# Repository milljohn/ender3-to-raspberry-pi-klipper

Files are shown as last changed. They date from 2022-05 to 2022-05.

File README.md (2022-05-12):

# ender3-to-raspberry-pi-klipper

Raspberry Pi Zero hat that supplies power via Ender 3V2 LCD cable for Klipper. NOTE: this seems to only work a Pi Zero, not a Pi 4. Not tested with a Pi 3 yet.

I made a quick version of this on protoboard, but I'm planning on making a few of these for printers at work and I wanted something a little cleaner and easier to put together.

I originally designed this as a hat, but after thinking about the prototype, it would be better just to make an adapter with crimp connectors.

This was originally posted [here](https://www.reddit.com/r/klippers/comments/q5cu20/how_to_connect_creality_v422_board_to_pi_using/).

## The PCB

The latest version is pi_hat_v2, though it is no longer a hat. I generated the cam files in pcb_files.zip. You can see the rendering below.

### Components
- 1 - 5 position, 2.54mm pitch female (socket) header
- 1 - 10 position, 2 rows, 2.54mm pitch male (pin) 90 degree header

NOTE: I used a 90 degree header so the drawer would close. It will work with straight headers, but you may have clearance issues.

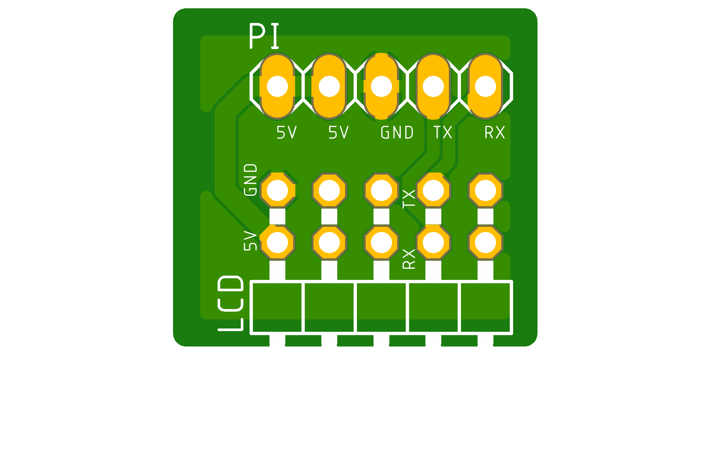
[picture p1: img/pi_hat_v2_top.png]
board top

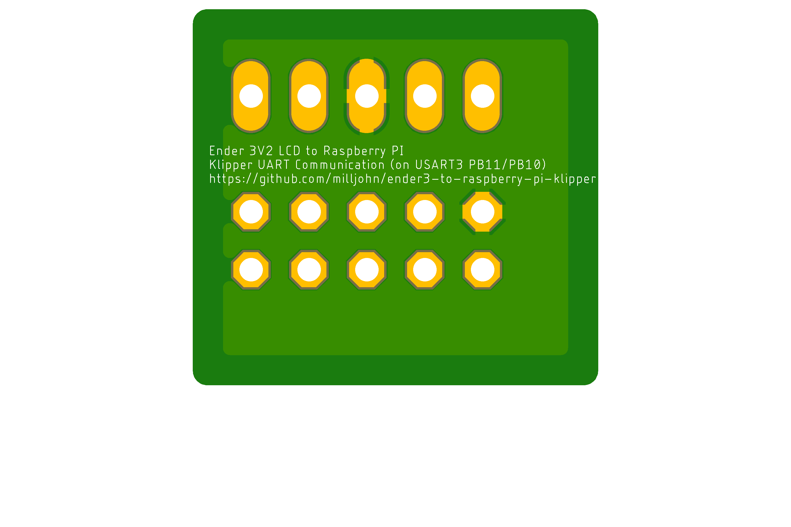
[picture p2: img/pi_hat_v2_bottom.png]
board bottom


## Klipper Configuration
If you are just starting out, [this guide](https://www.reddit.com/r/klippers/comments/kj2h5r/stepbystep_guide_for_ender_3_v2_klipper_w_bltouch/) will probably be helpful. I've tried to document the steps I took to [setup my printer](#fluidd-pi-configuration)

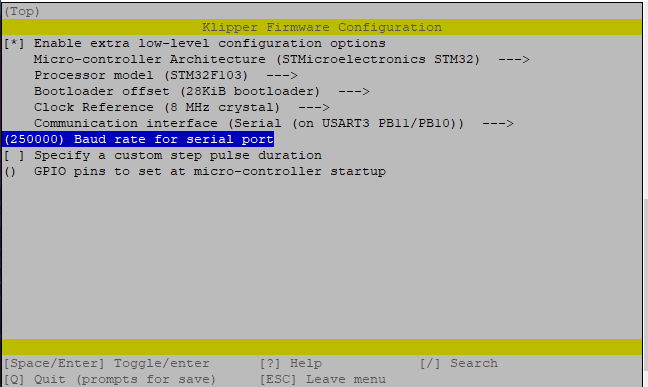
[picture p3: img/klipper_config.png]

[Klipper Firmware Configuration](https://i.imgur.com/JYTF8Xj.png)

Add ``serial = /dev/ttyAMA0`` to `printer.cfg`. Your serial port might be different. You can check by power on the Pi via USB and typing `ls /dev` and then comparing it to the list when connected with the ribbon cable. Mine was actually `/dev/ttyS0`. 

## Rasperry Pi Configuration
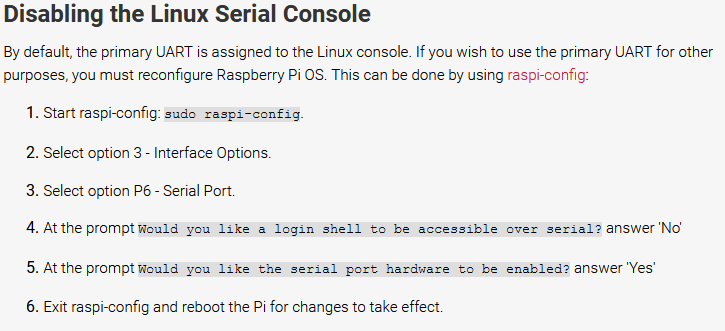
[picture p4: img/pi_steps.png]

[Disabling the Linux Serial Console](https://i.imgur.com/P6BS6GC.png)

This may be needed as well:
```shell
sudo echo dtoverlay=disable-bt >> /boot/config.txt
```

## Ender 3V2 Drawer 
I really like this drawer mount.

[Ender 3 v2 Hidden OctoPi Mount](https://www.thingiverse.com/thing:5201485)

Pi Zero drawer mount

## Fluidd Pi Configuration

These are the steps I took to setup Fluidd Pi

1. Burn Fluidd Pi [image](https://github.com/fluidd-core/FluiddPi/releases/latest) to SD Card 
2. Boot the Raspberry Pi
    - Add ssh keys to pi and update `~/.ssh/config`
      - on host: `ssh-keygen -t rsa -b 4096`, I chose no password and saved the file as 3dprinters
      - `mv ~/.ssh/3dprinters ~/.ssh/3dprinters.pem`
      - add the following to ~/.ssh/config
      ```
      host ender3.1
      hostname <raspi-ip-address>
      identityfile ~/.ssh/3dprinters.pem
      user pi

      ```
      - copy the public key to the pi
      ```
      sftp ender3.1
      mkdir -p .ssh
      put ~/.ssh/3dprinters.pub
      bye

      ssh ender3.1
      cd .ssh
      cat 3dprinters.pub >> authorized_keys
      exit
      ```
      - next time you `ssh ender3.1` it will login without a password.

    - `cd klipper && make menuconfig && make`
        - the default for usb is as follows
        
            1. Uncheck `Enable extra low-level configuration options`.
            2. Set processor architecture to `STMicroelectronics STM32`.
            3. Set processor model to `STM32F103`.
            4. Set bootloader offset to `28KiB bootloader`.
            5. Uncheck the other two options (`Use USB` and `Use CAN`).
            6. Save and exit.
        - if setting up serial over LCD cable, use the guide at the top of the page.
    - sftp and copy `~/klipper/out/klipper.bin` to SD card
        - insert into printer and turn on
    - run `~/moonraker/scripts/set-policykit-rules.sh`
    - `cp ~/klipper/config/printer-creality-ender3-v2-2020.cfg ~/klipper_config/printer.cfg`
    - add the lines below to `~/klipper_config/printer.cfg`
    - go to `http://<raspberrypi-ip-address>`
        - Check that everything is working with USB or serial
        - Tail logs, `tail -f ~/klipper_logs/klippy.log` and `tail -f ~/klipper_logs/moonraker.log`
3. `sudo raspi-config`
    - System options
        - setup wireless lan if you didn't already
        - change the default password
        - change the hostname if you want
    - Interface Option
        - ssh
        - serial port
            - no login over serial
            - enable hardware serial port
        - localization options (optional)
            - set to utf-8 and local timezome
    - reboot
    - run `sudo apt update && sudo apt upgrade -y`
4. Check the web interface to see if everything is working
    - check logs if something isn't working

Add this to the `printer.cfg`. I'm not sure why it isn't there by default, but it was frustrating trying to figure out that this was needed.
```
[virtual_sdcard]
path: ~/gcode_files

[display_status]

[pause_resume]

[gcode_macro PAUSE]
description: Pause the actual running print
rename_existing: PAUSE_BASE
# change this if you need more or less extrusion
variable_extrude: 1.0
gcode:
  ##### read E from pause macro #####
  {% set E = printer["gcode_macro PAUSE"].extrude|float %}
  ##### set park positon for x and y #####
  # default is your max posion from your printer.cfg
  {% set x_park = printer.toolhead.axis_maximum.x|float - 5.0 %}
  {% set y_park = printer.toolhead.axis_maximum.y|float - 5.0 %}
  ##### calculate save lift position #####
  {% set max_z = printer.toolhead.axis_maximum.z|float %}
  {% set act_z = printer.toolhead.position.z|float %}
  {% if act_z < (max_z - 2.0) %}
      {% set z_safe = 2.0 %}
  {% else %}
      {% set z_safe = max_z - act_z %}
  {% endif %}
  ##### end of definitions #####
  PAUSE_BASE
  G91
  {% if printer.extruder.can_extrude|lower == 'true' %}
    G1 E-{E} F2100
  {% else %}
    {action_respond_info("Extruder not hot enough")}
  {% endif %}
  {% if "xyz" in printer.toolhead.homed_axes %}
    G1 Z{z_safe} F900
    G90
    G1 X{x_park} Y{y_park} F6000
  {% else %}
    {action_respond_info("Printer not homed")}
  {% endif %}

[gcode_macro RESUME]
description: Resume the actual running print
rename_existing: RESUME_BASE
gcode:
  ##### read E from pause macro #####
  {% set E = printer["gcode_macro PAUSE"].extrude|float %}
  #### get VELOCITY parameter if specified ####
  {% if 'VELOCITY' in params|upper %}
    {% set get_params = ('VELOCITY=' + params.VELOCITY)  %}
  {%else %}
    {% set get_params = "" %}
  {% endif %}
  ##### end of definitions #####
  {% if printer.extruder.can_extrude|lower == 'true' %}
    G91
    G1 E{E} F2100
  {% else %}
    {action_respond_info("Extruder not hot enough")}
  {% endif %}  
  RESUME_BASE {get_params}

[gcode_macro CANCEL_PRINT]
description: Cancel the actual running print
rename_existing: CANCEL_PRINT_BASE
gcode:
  TURN_OFF_HEATERS
  CANCEL_PRINT_BASE
```

moonraker.conf
```
[server]
host: 0.0.0.0
port: 7125
enable_debug_logging: False

[file_manager]
config_path: ~/klipper_config
log_path: ~/klipper_logs

[data_store]
temperature_store_size: 600
gcode_store_size: 1000

[authorization]
force_logins: True
cors_domains:
  *.local
  *.lan
  *://app.fluidd.xyz

trusted_clients:
  10.0.0.0/8
  127.0.0.0/8
  169.254.0.0/16
  172.16.0.0/12
  192.168.0.0/16
  FE80::/10
  ::1/128

# enables partial support of Octoprint API
[octoprint_compat]

# enables moonraker to track and store print history.
[history]

# this enables moonraker's update manager
[update_manager]
enable_auto_refresh: True

# this enabled fluidd updates
[update_manager client fluidd]
type: web
repo: fluidd-core/fluidd
path: ~/fluidd
```

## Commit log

2022-05-05 inital layout
    [pi_hat.brd, pi_hat.sch]
2022-05-12 minor board revision
    [pi_hat_v2.brd, pi_hat_v2.sch]
